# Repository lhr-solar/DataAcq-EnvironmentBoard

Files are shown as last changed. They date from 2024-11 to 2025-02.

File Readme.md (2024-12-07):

# DataAcq-EnvironmentBoard
Author: Ravi Shah  
Documentation: https://cloud.wikis.utexas.edu/wiki/spaces/LHRSOLAR/pages/205226271/Data+Acquisition+Environment+Board

The Data Acquisition Environment Board measures environmental data throughout the car, including relative humidity, airflow, and temperature. It interfaces with a Peripheral System-On-Module (SOM) to process data and transmit it via the Data Acquisition CAN bus.

## BOM
IBOM: Hardware/BOM/ibom.html (download and view in browser)  
Mouser Cart: https://www.mouser.com/ProjectManager/ProjectDetail.aspx?AccessID=8fef7b51e5

## Connectors
| # | Name | Type | Ideal Voltage | Notes |
| - | - | - | - | - |
| U4  | PSOM Connection | 53307-2471 Female |N/A | 3.65mm tall |
| J2  | CAN Output | MicroFit3.0_1x4xP3.00mm_PolarizingPeg_Vertical Female |+12V | 6.98mm tall |
| J3  | CAN Input | MicroFit3.0_1x4xP3.00mm_PolarizingPeg_Vertical Female | +12V | 6.98mm tall |
| J6  | Breakout | Nano-Fit_105310-xx10_2x05_P2.50mm_Vertical Female | +3.3V | 9.05mm tall |

## PCB


## Schematic


## Additional Notes
- I know the connectors aren't numbered right, will fix in next iteration.  
- For production use (on the car), each main environment board will interface with a breakout board containing relevant sensors to the system being monitored. Wire harnessing should minimize the distance between the main board and the breakout to prevent noise. Main boards will be connected via EnvironmentCAN to each other and to the Data Acquisition leader board.
- Not all sensors need to be present, only necessary sensors should be soldered to the board/breakout according to system needs.

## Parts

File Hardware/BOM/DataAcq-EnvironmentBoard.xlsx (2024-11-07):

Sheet: Full BOM
Reference | Value | Footprint | Qty | P/N
D1,D2 | -- mixed values -- | LED_SMD:LED_0805_2012Metric | 2 | APTD2012LCGCK
D3,D4,D5,D6 | ESD9B | Diode_SMD:D_SOD-923 | 4 | ESD9B3.3ST5G
F1,F2,F3 | 250mA | Fuse:Fuse_0603_1608Metric | 3 | 0ZCM0010FF2G
J2,J3 | -- mixed values -- | UTSVT_Connectors:Molex_MicroFit3.0_1x4xP3.00mm_PolarizingPeg_Vertical | 2 | 436500244
J6 | Breakout Connector | Connector_Molex:Molex_Nano-Fit_105310-xx10_2x05_P2.50mm_Vertical | 1 | 1053101110
R2 | 22.1k | Resistor_SMD:R_0805_2012Metric | 1 | CRCW080522K1FKEA
R3 | 2.2k | Resistor_SMD:R_0805_2012Metric | 1 | SDR10EZPF2200
U1 | FS3000-1005 | SamacSys_Parts:FS30001005 | 1 | FS3000-1005
U2 | LMT87DCK | Package_TO_SOT_SMD:SOT-353_SC-70-5 | 1 | LMT87QDCKRQ1
U3 | SHT45 | Sensor_Humidity:Sensirion_DFN-4_1.5x1.5mm_P0.8mm_SHT4x_NoCentralPad | 1 | SHT45-AD1B-R3
U4 | Daughterboard Connector | UTSVT_Special:PeripheralSOM | 1 | 53307-2471

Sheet: Shortened BOM
Reference | Value | Footprint | Qty | P/N
U1 | FS3000-1005 | SamacSys_Parts:FS30001005 | 1 | FS3000-1005
U2 | LMT87DCK | Package_TO_SOT_SMD:SOT-353_SC-70-5 | 1 | LMT87QDCKRQ1
U3 | SHT45 | Sensor_Humidity:Sensirion_DFN-4_1.5x1.5mm_P0.8mm_SHT4x_NoCentralPad | 1 | SHT45-AD1B-R3
U4 | Daughterboard Connector | UTSVT_Special:PeripheralSOM | 1 | 53307-2471
D3,D4,D5,D6 | ESD9B | Diode_SMD:D_SOD-923 | 4 | ESD9B3.3ST5G
F1,F2,F3 | 250mA | Fuse:Fuse_0603_1608Metric | 3 | 0ZCM0010FF2G
J6 | Breakout Connector | Connector_Molex:Molex_Nano-Fit_105310-xx10_2x05_P2.50mm_Vertical | 1 | 1053101110

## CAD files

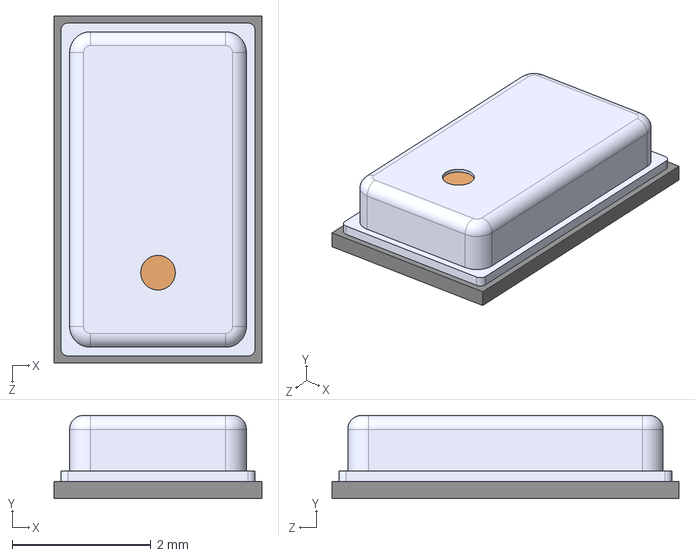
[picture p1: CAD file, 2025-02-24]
Hardware/Custom-KiCadLibraries/MPL3115A2S/MPL3115A2--3DModel-STEP-269445.STEP
3.00 x 1.20 x 5.00 mm

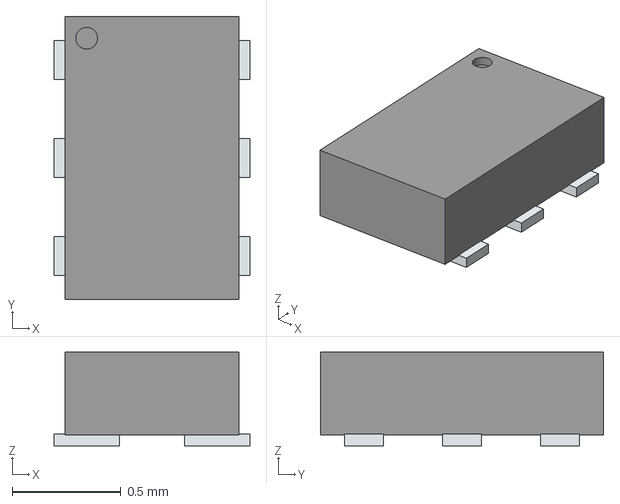
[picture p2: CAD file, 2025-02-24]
Hardware/Custom-KiCadLibraries/PESD3V3L4BHCYL/PESD3V3L4BHCYL.stp
0.9 x 1.30 x 0.43 mm
PinsArrayLR

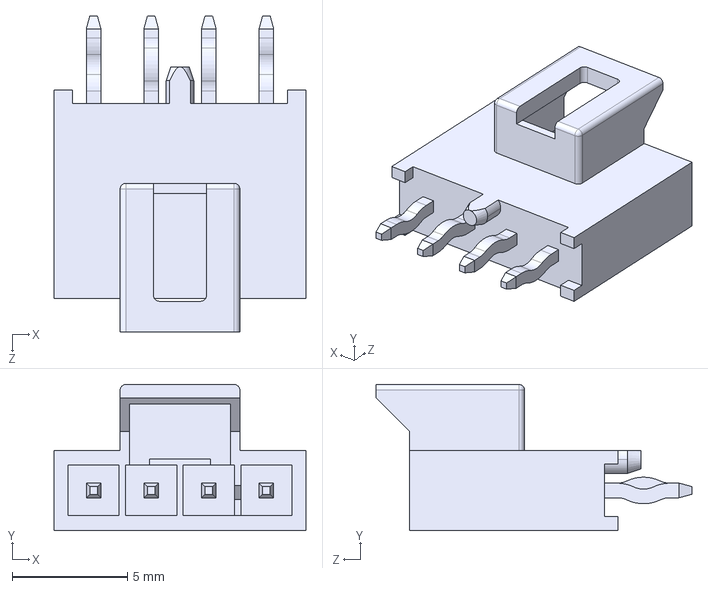
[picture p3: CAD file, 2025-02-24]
Hardware/Custom-KiCadLibraries/1053091104/1053091104.step
10.9 x 6.34 x 13.7 mm

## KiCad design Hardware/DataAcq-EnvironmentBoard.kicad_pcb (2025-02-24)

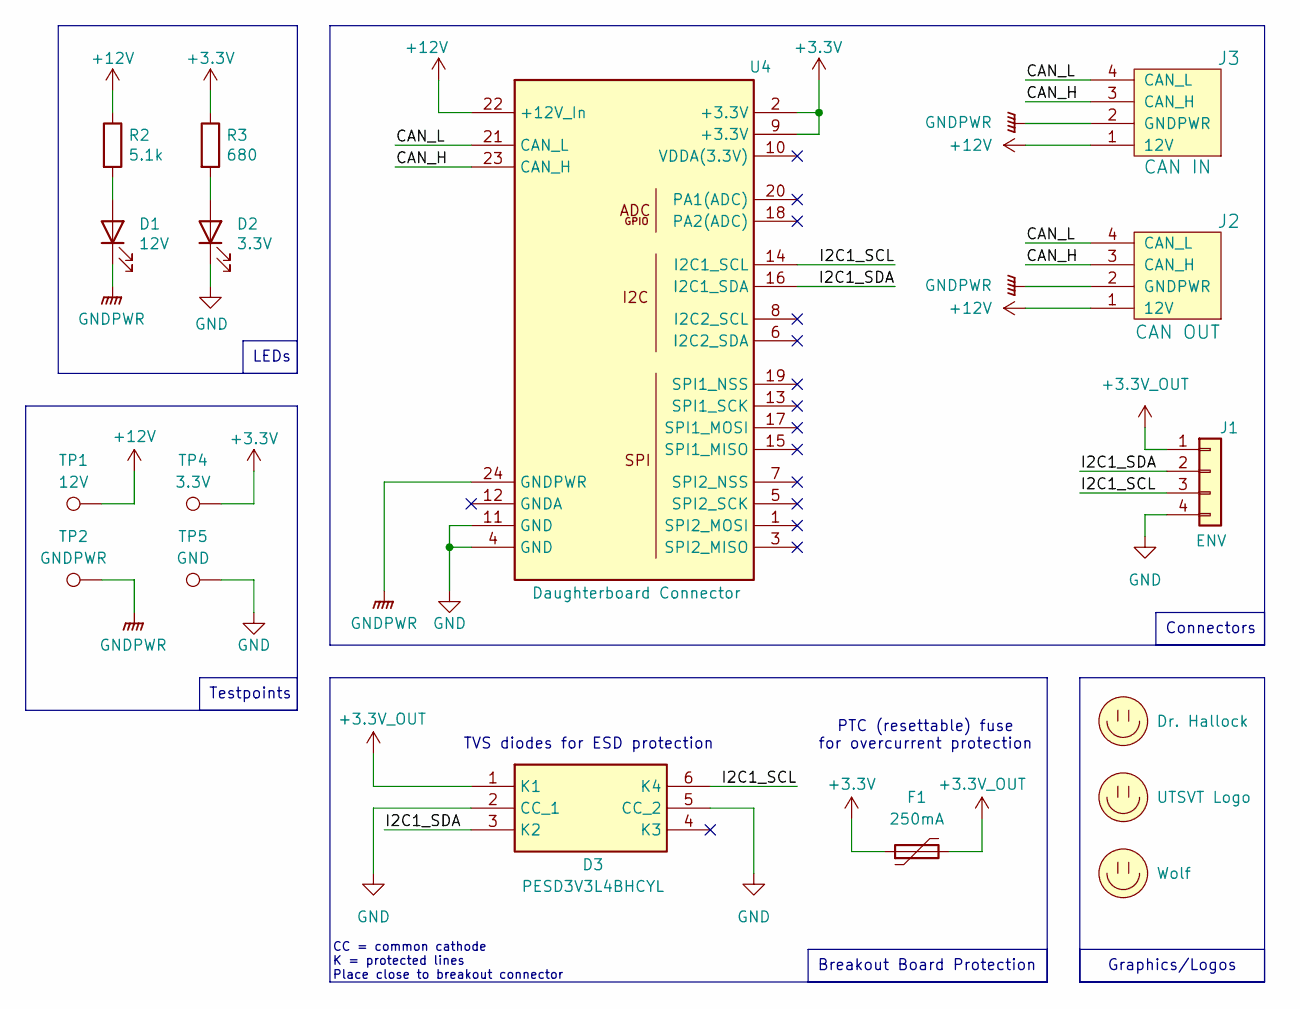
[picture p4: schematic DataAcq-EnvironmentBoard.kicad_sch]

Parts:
D1: 12V; LED_0805_2012Metric; Mouser Part Number 604-APTD2012LCGCK
D2: 3.3V; LED_0805_2012Metric; Mouser Part Number 604-APTD2012LCGCK
D3: PESD3V3L4BHCYL; SON45P80X130X43-6N; Manufacturer_Part_Number PESD3V3L4BHCYL; Mouser Part Number 771-PESD3V3L4BHCYL
F1: 250mA; Fuse_1206_3216Metric
J1: ENV; MOLEX_1053091104
J2: CAN OUT; Molex_MicroFit3.0_1x4xP3.00mm_PolarizingPeg_Vertical
J3: CAN IN; Molex_MicroFit3.0_1x4xP3.00mm_PolarizingPeg_Vertical
LOGO2: Dr. Hallock; Hallock_Image_Tiny
LOGO3: UTSVT Logo; UTSVT_Logo_Symbol
LOGO4: Wolf; wolf
R2: 5.1k; R_0805_2012Metric; Mouser Part Number 71-CRCW0805-22.1K-E3
R3: 680; R_0805_2012Metric; Mouser Part Number Inventory
TP1: 12V; TestPoint_HEX_3mmID
TP2: GNDPWR; TestPoint_HEX_3mmID
TP4: 3.3V; TestPoint_HEX_3mmID
TP5: GND; TestPoint_HEX_3mmID
U4: Daughterboard Connector; PeripheralSOM

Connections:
+3.3V: F1.1, R3.1, TP4.1, U4.2 (+3.3V), U4.9 (+3.3V)
+3.3V_OUT: D3.1 (K1), F1.2, J1.1
+12V: J2.1 (12V), J3.1 (12V), R2.1, TP1.1, U4.22 (+12V_In)
/CAN_H: J2.3 (CAN_H), J3.3 (CAN_H), U4.23 (CAN_H)
/CAN_L: J2.4 (CAN_L), J3.4 (CAN_L), U4.21 (CAN_L)
/I2C1_SCL: D3.6 (K4), J1.3, U4.14 (I2C1_SCL)
/I2C1_SDA: D3.3 (K2), J1.2, U4.16 (I2C1_SDA)
GND: D2.1 (K), D3.2 (CC_1), D3.5 (CC_2), J1.4, TP5.1, U4.4 (GND), U4.11 (GND)
GNDPWR: D1.1 (K), J2.2 (GNDPWR), J3.2 (GNDPWR), TP2.1, U4.24 (GNDPWR)
unnamed: D1.2 (A), R2.2
unnamed: D2.2 (A), R3.2

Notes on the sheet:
Breakout Board Protection
LEDs
Connectors
Testpoints
Graphics/Logos
CC = common cathode K = protected lines Place close to breakout connector
PTC (resettable) fuse for overcurrent protection
TVS diodes for ESD protection

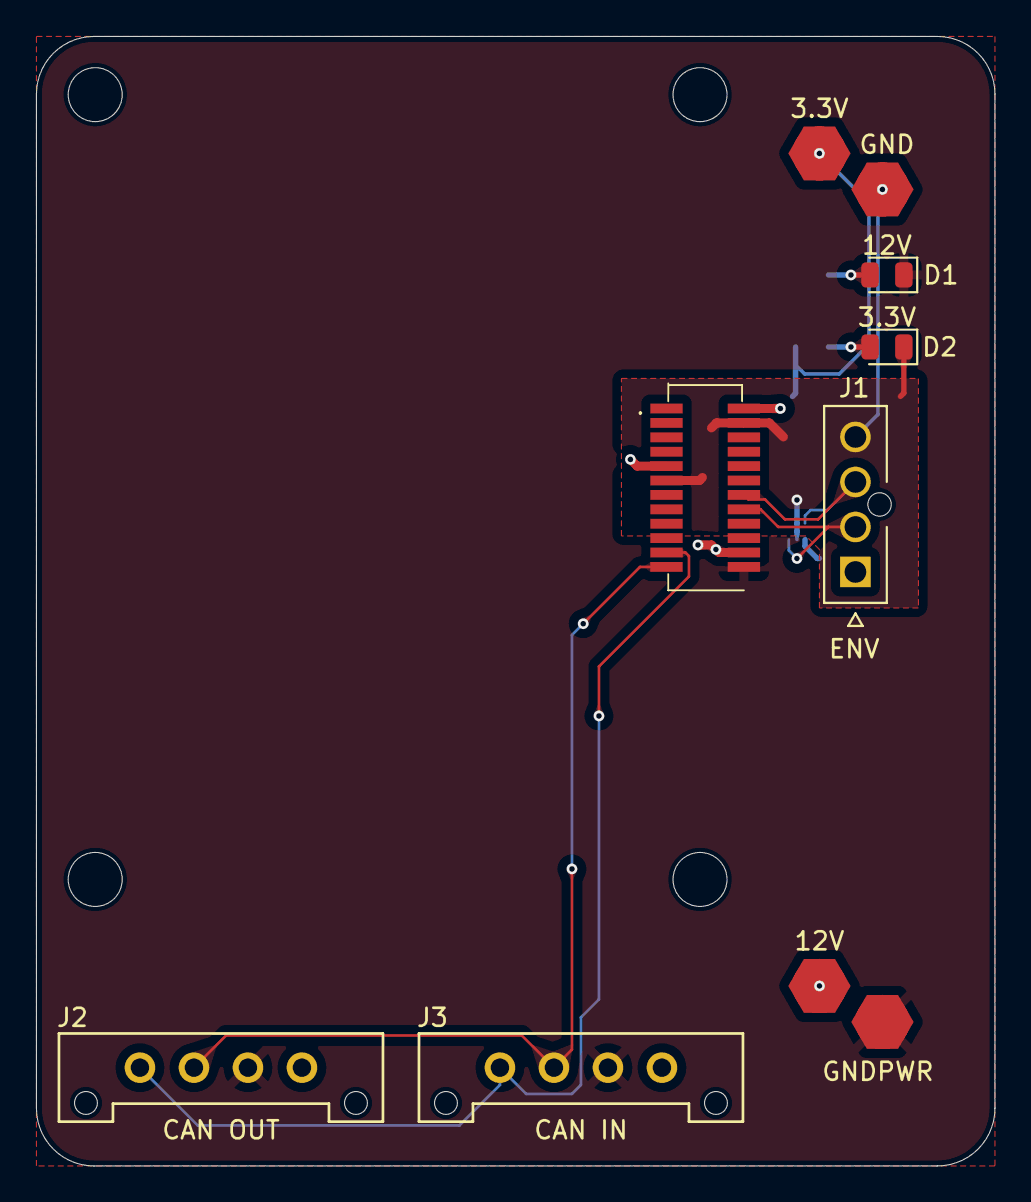
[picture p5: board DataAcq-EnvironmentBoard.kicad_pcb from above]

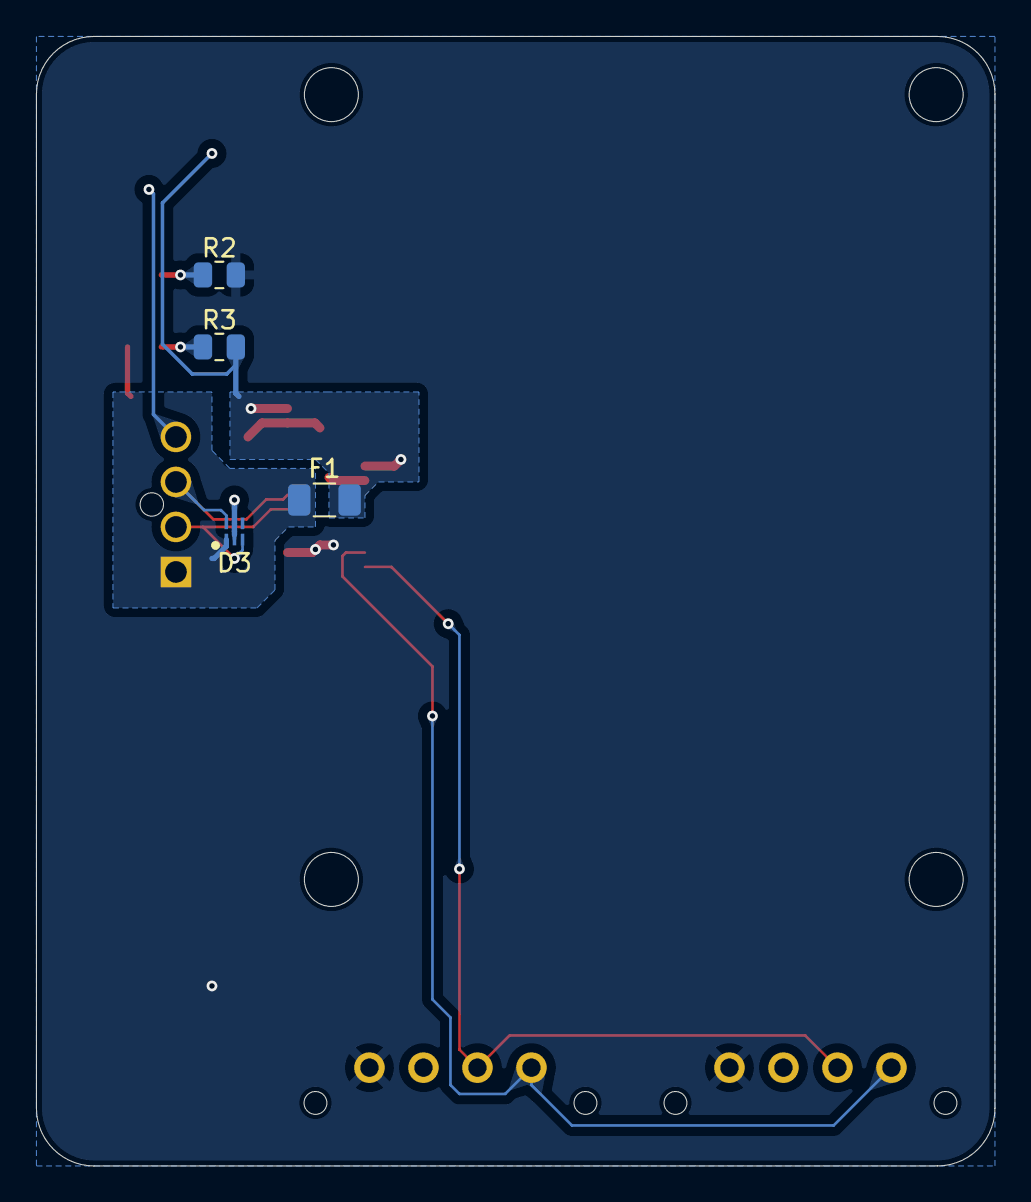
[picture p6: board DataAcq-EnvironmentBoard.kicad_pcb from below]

Board: 2 copper layers, 53.2 x 62.8 mm, 17 parts (4 on the bottom side), 11 nets.

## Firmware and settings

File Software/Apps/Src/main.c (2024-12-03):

// TODO: move both i2c and CAN to separate files

/* Includes ------------------------------------------------------------------*/
#include "main.h"
#include "string.h"
#include "stm32xx_hal.h"

// Initialize variables
uint8_t final_temp; // final temp from SHT45
uint8_t final_rh;   // final rh from SHT45

struct SHT45_Poll_Result // final temp/rh result of polling SHT45 sensor
{
    uint8_t final_temp;
    uint8_t final_rh;
};

StaticTask_t task_buffer;
StackType_t taskStack[configMINIMAL_STACK_SIZE];

/* Private function prototypes -----------------------------------------------*/
void SystemClock_Config(void);
void MX_I2C1_Init(void);
void MX_I2C2_Init(void);
void MX_CAN_Init(void);

struct SHT45_Poll_Result poll_SHT45(void);

void send_payload_CAN(uint8_t final_temp, uint8_t final_rh);

static void task(void *pvParameters);
void error_handler(void);
static void success_handler(void);

int main(void)
{
    // initialize the HAL and system clock
    if (HAL_Init() != HAL_OK)
        error_handler();

    /* Initialize all configured peripherals */
    MX_I2C1_Init();
    MX_I2C2_Init();
    MX_CAN_Init();

    xTaskCreateStatic(
        task,
        "task",
        configMINIMAL_STACK_SIZE,
        NULL,
        tskIDLE_PRIORITY + 2,
        taskStack,
        &task_buffer);

    vTaskStartScheduler();

    error_handler();

    return 0;
}

// for when actual (non-sensor) errors are encountered - mainly CAN transmission
void error_handler(void)
{
    __disable_irq();
    while (1)
    {
        // TODO: do smth useful here?
    }
}

// blinks LED upon successful CAN transmission
static void success_handler(void)
{
    GPIO_InitTypeDef led_init = {
        .Mode = GPIO_MODE_OUTPUT_PP,
        .Pull = GPIO_NOPULL,
        .Pin = GPIO_PIN_5};

    __HAL_RCC_GPIOA_CLK_ENABLE();
    HAL_GPIO_Init(GPIOA, &led_init);

    HAL_GPIO_TogglePin(GPIOA, GPIO_PIN_5);
    HAL_Delay(500);
    HAL_GPIO_TogglePin(GPIOA, GPIO_PIN_5);
    HAL_Delay(500);
}

static void task(void *pvParameters)
{
    while (1)
    {
        struct SHT45_Poll_Result final_SHT45_result = poll_SHT45(); // poll SHT45 sensor for temp/rh values
        final_temp = final_SHT45_result.final_temp;
        final_rh = final_SHT45_result.final_rh;

        send_payload_CAN(final_temp, final_rh); // package and send CAN payload according to environment specs
        success_handler();                      // blink LED upon successful message transmission
    }
}

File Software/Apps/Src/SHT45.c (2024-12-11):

// driver for Sensirion SHT45 temperature & relative humidity sensor (on I2C1)
// provides functionality for temp/rh measurement & checksum validation

/* Includes ------------------------------------------------------------------*/
#include "main.h"
#include "I2C.h"
#include "stm32xx_hal.h"
#include "SHT45.h"

// Initialize variables
I2C_HandleTypeDef hi2c1;

uint8_t TX_Buffer[1] = {0xFD}; // Data to send to request reading from humidity sensor

uint16_t temp_ticks;  // raw temp data received from SHT45
uint8_t temp_degC;    // temp value in celsius
uint16_t rh_ticks;    // raw rh data received from SHT45
uint8_t rh_percentRH; // rh value as percentage

uint16_t checksum_temp;            // checksum for temp received from SHT45
uint16_t checksum_rh;              // checksum for rh received from SHT45
const uint16_t crc_poly = 0x31;    // polynomial used to calculate checksum for SHT45 (from datasheet)
const uint16_t crc_initial = 0xFF; // initial CRC value for SHT45 (from datasheet)

enum SHT45_CRC_Result // potential values for CRC result for SHT45
{
    VALID = 0,
    TEMP_VALID = 1,
    RH_VALID = 2,
    INVALID = 3
};

struct SHT45_Poll_Result // final temp/rh result of polling SHT45 sensor to return
{
    uint8_t final_temp;
    uint8_t final_rh;
};

// function prototypes
static enum SHT45_CRC_Result SHT45_CRC(uint8_t RX_Buffer[6]);

// I2C1 initialization function
void MX_I2C1_Init(void)
{
    // init i2c parameters
    hi2c1.Instance = I2C1;
    hi2c1.Init.ClockSpeed = 100000;
    hi2c1.Init.DutyCycle = I2C_DUTYCYCLE_2;
    hi2c1.Init.OwnAddress1 = 0;
    hi2c1.Init.AddressingMode = I2C_ADDRESSINGMODE_7BIT;
    hi2c1.Init.DualAddressMode = I2C_DUALADDRESS_DISABLE;
    hi2c1.Init.OwnAddress2 = 0;
    hi2c1.Init.GeneralCallMode = I2C_GENERALCALL_DISABLE;
    hi2c1.Init.NoStretchMode = I2C_NOSTRETCH_DISABLE;

    // error handling disabled since we don't know which sensors will be soldered onto each board
    // if a sensor isn't present, expected behavior is to pad with zeros (no error msg)

    HAL_I2C_Init(&hi2c1);

    /*if (HAL_I2C_Init(&hi2c1) != HAL_OK)
    {
        error_handler();
    }*/

    // Configure Analog filter
    HAL_I2CEx_ConfigAnalogFilter(&hi2c1, I2C_ANALOGFILTER_ENABLE);

    /*if (HAL_I2CEx_ConfigAnalogFilter(&hi2c1, I2C_ANALOGFILTER_ENABLE) != HAL_OK)
    {
        error_handler();
    }*/

    // Configure Digital filter
    HAL_I2CEx_ConfigDigitalFilter(&hi2c1, 0);

    /*if (HAL_I2CEx_ConfigDigitalFilter(&hi2c1, 0) != HAL_OK)
    {
        error_handler();
    }*/
}

// poll SHT45 sensor for temperature and relative humidity, return zeros upon error
struct SHT45_Poll_Result poll_SHT45(void)
{
    // reset temp/rh vars
    temp_ticks = 0;
    rh_ticks = 0;
    uint8_t RX_Buffer[6] = {0}; // Data received from humidity sensor

    HAL_I2C_Master_Transmit(&hi2c1, (uint16_t)(0x44 << 1), TX_Buffer, sizeof TX_Buffer, 1000); // Sending in Blocking mode
    HAL_Delay(10);                                                                             // wait for 0.01 seconds (datasheet value) for response from sensor
    HAL_I2C_Master_Receive(&hi2c1, (uint16_t)(0x44 << 1), RX_Buffer, sizeof RX_Buffer, 50);

    // parse received data for temperature
    temp_ticks = (RX_Buffer[0] * 256) + RX_Buffer[1];
    temp_degC = (-45 + (175 * temp_ticks / 65535));

    // parse received data for relative humidity
    rh_ticks = (RX_Buffer[3] * 256) + RX_Buffer[4];
    rh_percentRH = (-6 + (125 * rh_ticks / 65535));

    // if percent rh is < 0, set to 0. if percent rh is > 100, set to 100 (expected behavior from SHT45 datasheet)
    if (rh_percentRH < 0)
    {
        rh_percentRH = 0;
    }
    else if (rh_percentRH > 100)
    {
        rh_percentRH = 100;
    }

    // handle CRC result
    enum SHT45_CRC_Result SHT45_valid = SHT45_CRC(RX_Buffer); // calculate and verify CRC - returns value according to enum above
    // any invalid values are sent as zeros as per DataAcq specs
    if (SHT45_valid == TEMP_VALID)
    {
        rh_percentRH = 0;
    }
    else if (SHT45_valid == RH_VALID)
    {
        temp_degC = 0;
    }
    else if (SHT45_valid == INVALID)
    {
        temp_degC = 0;
        rh_percentRH = 0;
    }

    struct SHT45_Poll_Result r = {temp_degC, rh_percentRH};
    return r;
}

// calculate and verify CRC-8 for the SHT45 humidity sensor
static enum SHT45_CRC_Result SHT45_CRC(uint8_t RX_Buffer[6])
{
    checksum_temp = 0;
    checksum_rh = 0;
    uint8_t computed_temp_crc;
    uint8_t computed_rh_crc;
    enum SHT45_CRC_Result SHT45_valid = INVALID; // set result to INVALID by default

    // use checksum to verify data is received correctly - important when we use the breakout boards as that may introduce noise on i2c bus
    checksum_temp = RX_Buffer[2];

    // TEST: manually set known values... checksum of 0xBEEF = 0x92 (according to SHT45 datasheet)
    // RX_Buffer[0] = 0xBE;
    // RX_Buffer[1] = 0xEF;
    // checksum_temp = 0x92;

    // manually implemented using algo at https://www.st.com/resource/en/application_note/an4187-using-the-crc-peripheral-on-stm32-microcontrollers-stmicroelectronics.pdf
    // sequentially (thanks chatgpt :D) - do the crc for first byte first and then use that val as input data for the crc for second byte and should give you proper value, verify this with what we actually recieve from the sensor

    computed_temp_crc = crc_initial ^ RX_Buffer[0]; // 1st step of CRC for 1st temp byte

    // calc crc for first byte
    for (uint8_t bindex = 0; bindex < sizeof(RX_Buffer[0]) * 8; bindex++)
    {
        uint8_t MSB = (int8_t)computed_temp_crc < 0; // get MSB of CRC

        if (MSB == 1)
        {
            computed_temp_crc = (computed_temp_crc << 1) ^ crc_poly; // shift one bit left, XOR with poly
        }
        else
        {
            computed_temp_crc = computed_temp_crc << 1; // shift one bit left
        }
    }

    // sequential calc for second byte (using first byte crc as initial crc)
    computed_temp_crc = computed_temp_crc ^ RX_Buffer[1]; // 1st step of CRC for 2nd temp byte

    for (uint8_t bindex = 0; bindex < sizeof(RX_Buffer[1]) * 8; bindex++)
    {
        uint8_t MSB = (int8_t)computed_temp_crc < 0; // get MSB of CRC

        if (MSB == 1)
        {
            computed_temp_crc = (computed_temp_crc << 1) ^ crc_poly; // shift one bit left, XOR with poly
        }
        else
        {
            computed_temp_crc = computed_temp_crc << 1; // shift one bit left
        }
    }

    // same calulcation for rh bytes
    checksum_rh = RX_Buffer[5];

    computed_rh_crc = crc_initial ^ RX_Buffer[3]; // 1st step of CRC for 1st rh byte

    // calc crc for first byte
    for (uint8_t bindex = 0; bindex < sizeof(RX_Buffer[3]) * 8; bindex++)
    {
        uint8_t MSB = (int8_t)computed_rh_crc < 0; // get MSB of CRC
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

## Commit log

2024-10-05 create initial KiCad project
    [DataAcq-EnvironmentBoard.kicad_pcb, DataAcq-EnvironmentBoard.kicad_sch]
2024-10-05 add schematic for humidity, airfow, temp sensors
    [DataAcq-EnvironmentBoard.kicad_sch]
2024-10-11 add connector for PSOM
    [DataAcq-EnvironmentBoard.kicad_sch]
2024-10-12 add CAN connector
    [DataAcq-EnvironmentBoard.kicad_sch]
2024-10-12 add second CAN connector and fix analog gnd
    [DataAcq-EnvironmentBoard.kicad_sch]
2024-10-12 thanks lakshay
    [DataAcq-EnvironmentBoard.kicad_sch]
2024-10-12 start laying stuff out
    [DataAcq-EnvironmentBoard.kicad_pcb, DataAcq-EnvironmentBoard.kicad_sch]
2024-10-12 fix labels
    [DataAcq-EnvironmentBoard.kicad_sch]
2024-10-12 initial layout/routing
    [DataAcq-EnvironmentBoard.kicad_pcb, DataAcq-EnvironmentBoard.kicad_sch]
2024-10-14 layout again
    [DataAcq-EnvironmentBoard.kicad_pcb, DataAcq-EnvironmentBoard.kicad_sch]
2024-10-14 add LEDs/testpoints to sch
    [DataAcq-EnvironmentBoard.kicad_sch]
2024-10-14 test points
    [DataAcq-EnvironmentBoard.kicad_pcb, DataAcq-EnvironmentBoard.kicad_sch]
2024-10-14 part numbers smh
    [DataAcq-EnvironmentBoard.kicad_pcb, DataAcq-EnvironmentBoard.kicad_sch]
2024-10-14 fix ground pad
    [DataAcq-EnvironmentBoard.kicad_pcb]
2024-10-14 dumbass labels
    [DataAcq-EnvironmentBoard.kicad_sch]
2024-10-15 rework traces
    [DataAcq-EnvironmentBoard.kicad_pcb]
2024-10-15 group footprints properly
    [DataAcq-EnvironmentBoard.kicad_pcb]
2024-10-16 third times the charm (layout)
    [DataAcq-EnvironmentBoard.kicad_pcb, DataAcq-EnvironmentBoard.kicad_sch]
2024-10-17 better CAN routing
    [DataAcq-EnvironmentBoard.kicad_pcb, DataAcq-EnvironmentBoard.kicad_sch]
2024-10-17 remove extraneous label
    [DataAcq-EnvironmentBoard.kicad_sch]
2024-10-18 change sch to match new symbols
    [DataAcq-EnvironmentBoard.kicad_pcb, DataAcq-EnvironmentBoard.kicad_sch]
2024-10-18 fix thermal reliefs and fills
    [DataAcq-EnvironmentBoard.kicad_pcb]
2024-10-20 add test point and redo CAN connections
    [DataAcq-EnvironmentBoard.kicad_pcb, DataAcq-EnvironmentBoard.kicad_sch]
2024-10-22 add images and cleanup
    [DataAcq-EnvironmentBoard.kicad_pcb, DataAcq-EnvironmentBoard.kicad_sch]
2024-10-22 start adding dimensions (not final)
    [DataAcq-EnvironmentBoard.kicad_pcb]
2024-10-25 add i2c testpoints to sch
    [DataAcq-EnvironmentBoard.kicad_pcb, DataAcq-EnvironmentBoard.kicad_sch]
2024-10-26 move passives to sensor side, reroute temp sensor
    [DataAcq-EnvironmentBoard.kicad_pcb, DataAcq-EnvironmentBoard.kicad_sch]
2024-10-26 add breakout board connectors to sch
    [DataAcq-EnvironmentBoard.kicad_pcb, DataAcq-EnvironmentBoard.kicad_sch]
2024-10-26 add TVS diodes and fuses for breakout
    [DataAcq-EnvironmentBoard.kicad_sch]
2024-10-26 assign footprints and PN
    [DataAcq-EnvironmentBoard.kicad_sch]
2024-10-27 pls be the last time i have to layout this
    [DataAcq-EnvironmentBoard.kicad_pcb, DataAcq-EnvironmentBoard.kicad_sch]
2024-10-27 update BOM
    [DataAcq-EnvironmentBoard.kicad_sch, DataAcq-EnvironmentBoard.xlsx]
2024-10-29 rm useless stuff
    [DataAcq-EnvironmentBoard.kicad_pcb]
2024-10-29 start sch/layout modifications
    [DataAcq-EnvironmentBoard.kicad_pcb, DataAcq-EnvironmentBoard.kicad_sch]
2024-10-30 update BOM and model
    [DataAcq-EnvironmentBoard.kicad_pcb, DataAcq-EnvironmentBoard.kicad_sch, DataAcq-EnvironmentBoard.xlsx]
2024-10-30 fix trace routing
    [DataAcq-EnvironmentBoard.kicad_pcb]
2024-10-30 silkscreen info
    [DataAcq-EnvironmentBoard.kicad_pcb]
2024-10-31 change sch for one connector design
    [DataAcq-EnvironmentBoard-B_Cu.gbl, DataAcq-EnvironmentBoard-B_Paste.gbp, DataAcq-EnvironmentBoard-B_Silkscreen.gbo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]
2024-11-01 modify layout for new connector
    [DataAcq-EnvironmentBoard.kicad_pcb]
2024-11-02 sch: add sensors back for testing
    [DataAcq-EnvironmentBoard.kicad_sch]
2024-11-02 rearrange connector to match breakout
    [DataAcq-EnvironmentBoard.kicad_sch]
2024-11-02 traces for connector change
    [DataAcq-EnvironmentBoard.kicad_pcb, DataAcq-EnvironmentBoard.kicad_sch]
2024-11-02 fix silkscreen
    [DataAcq-EnvironmentBoard.kicad_pcb]
2024-11-03 fix pours
    [DataAcq-EnvironmentBoard.kicad_pcb]
2024-11-03 finalize layout
    [DataAcq-EnvironmentBoard.kicad_pcb]
2024-11-03 correct mounting hole dimensions
    [DataAcq-EnvironmentBoard.kicad_pcb]
2024-11-07 wtf git
    [DataAcq-EnvironmentBoard.kicad_pcb, DataAcq-EnvironmentBoard.xlsx]
2024-11-07 pls work
    [DataAcq-EnvironmentBoard.kicad_pcb]
2024-11-09 separate hardware and software
    [DataAcq-EnvironmentBoard-B_Cu.gbl, DataAcq-EnvironmentBoard-B_Paste.gbp, DataAcq-EnvironmentBoard-B_Silkscreen.gbo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]
2024-11-09 LED test
2024-11-14 add test i2c transmit
2024-11-18 move working i2c code to test folder
2024-11-23 specify format for CAN frames and pad with zeros upon error
    [main.c]
2024-12-02 add i2c2 init (for airflow)
2024-12-03 move SHT45 driver to separate file
2024-12-07 update readme with connectors/bom
2024-12-07 update readme with sch/pcb/notes
2024-12-11 start adding FS3000 driver, not verified yet
2025-02-24 remove sensors from this board
    [DataAcq-EnvironmentBoard.kicad_sch]
2025-02-24 rework sch for new breakout design
    [1053091104.step, DataAcq-EnvironmentBoard.kicad_sch, MPL3115A2--3DModel-STEP-269445.STEP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]
2025-02-24 new ptc & footprints
    [DataAcq-EnvironmentBoard.kicad_pcb, DataAcq-EnvironmentBoard.kicad_sch]
2025-02-24 dumb and dumber
    [DataAcq-EnvironmentBoard.kicad_sch]
2025-02-24 not layout
    [DataAcq-EnvironmentBoard.kicad_pcb]
2025-02-24 layout finished
    [DataAcq-EnvironmentBoard.kicad_pcb]
